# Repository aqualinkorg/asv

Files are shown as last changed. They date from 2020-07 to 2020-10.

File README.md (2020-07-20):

# Aqualink ASV

The Aqualink ASV is an open-source reference design for an autonomous surface vehicle. Included in this project are all hardware & electronics designs, software components, and instructions necessary to outfit a generic boat hull to navigate autonomously and collect camera and sensor data.

This project is designed around a collection of existing software projects, such as ROS2, Ardupilot, QGroundControl, and more. All hardware components are off-the-shelf with links to suppliers within the included [Bill of Materials](hardware/bill_of_materials.pdf) document. The construction process has been tailored to require no soldering and minimal, standard tools.

## Project Structure

The project is split into three main folders, each with their own setup guides:

- `groundstation/`: Contains setup instructions and software that will be run on a Linux laptop used to control the vehicle.
- `hardware/`: Contains all drawings & CAD (electrical and mechanical), assembly instructions and photos, and the bill of materials.
- `vehicle/`: Contains setup instructions and software for both the Nvidia Jetson Nano and Rambutan OpenWRT router that are installed in the vehicle electronics box.

While there is a great deal of flexibility in which order to read and follow the instructions, the order we recommend is:

1. Review all materials in `hardware/` to get an understanding of how everything fits together:
   - [Hardware Setup](hardware/README.md)
   - [System Diagram](hardware/drawings_and_cad/system_diagram.pdf)
   - [Electrical Connections](hardware/drawings_and_cad/electrical_connections.pdf)
   - [Bill of Materials](hardware/bill_of_materials.pdf)
2. Acquire all components, as specified by the BOM and your own project's requirements
3. Before assembling the hardware, set up the Nano and Rambutan router. These steps are easier pre-assembly:
   - [Nano Setup](vehicle/nano_setup.md)
   - [Router Setup](vehicle/router_setup.md)
4. Follow the instructions and drawings in the [Hardware Setup](hardware/README.md) to assemble the electronics and battery enclosures
5. Integrate the electronics and battery enclosures, motors, sensors, etc. into your vehicle hull
6. With the vehicle fully assembled, perform the [Pixhawk Setup](vehicle/pixhawk_setup.md)
7. At this point, your vehicle should be fully assembled, calibrated, and ready to deploy.

## Software Overview

Here is an image that shows the way all of the nodes connect together via ROS2 topics:

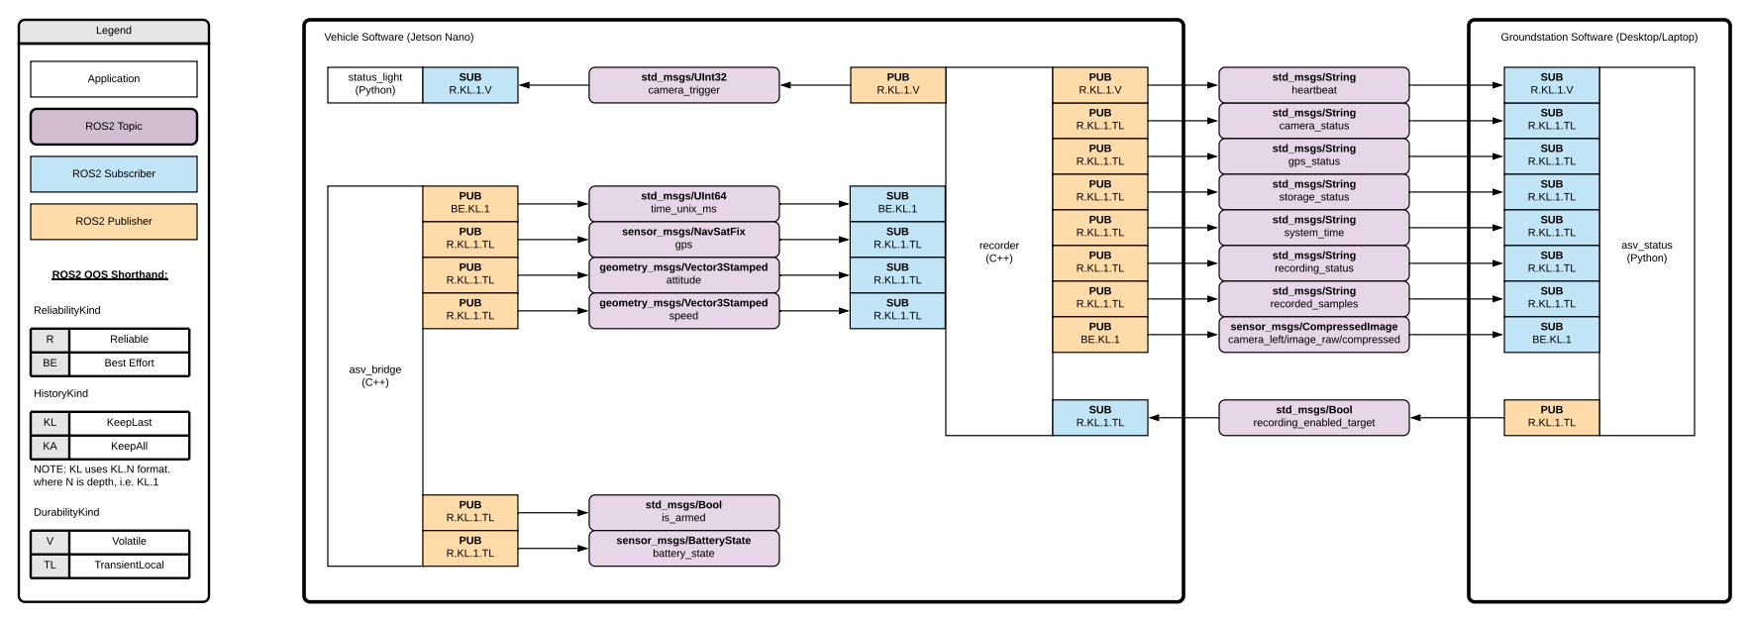
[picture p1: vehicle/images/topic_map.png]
topicmap


For more information on each software node, see:
  - [Groundstation Software](groundstation/README.md)
  - [Vehicle Software](vehicle/README.md)

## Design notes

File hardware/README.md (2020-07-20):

# Hardware Setup

## Pre-reqs
### Tools
- Drill + various drill bits (see drawings)
- Deburring tool (to clean up drill holes)
- Screwdriver set (phillips, slotted, hex)
- Crescent wrench (expands to at least 32mm)
- Needle nose pliers
- Scissors or flush cutters

### Parts
Refer to the [Bill of Materials (BOM)](bill_of_materials.pdf) for the list of parts

#### Not on Bill of Materials
- [Upper Plate](drawings_and_cad/upper_plate/) - This part can be laser cut out of 3mm thick material.
- [Power Mounting Block](drawings_and_cad/power_mounting_block/) - This part can be 3D printed
- Double sided tape (to secure Pixhawk)
- Grease (for o-rings)
- USB 3.0 SSD (for storing data)

## Assembly

### General Assembly Notes
- Make sure to lubricate all o-rings before installation
- M2.5x22mm screws (x4) are only used to attach the fan to the Jetson Nano

### Drill Enclosure
Refer to the [enclosure drawing](drawings_and_cad/enclosure/DRW-0023-01_PTS-25340-C_with_holes.pdf) for the location the holes should be drilled, as well as the hole diameter. The hole callouts are for clearance holes for parts to fit through. This means the sizes are less common. You can use a drill that is +/- 0.2mm without issue. Also, while all dimensions are metric, sometimes a standard drill bit will be a close match.

### Drill Bottom Plate
Refer to the [bottom plate drawing](drawings_and_cad/lower_plate/DRW-0019-01_PTV-25340_with_holes.pdf) for the location the holes should be drilled, as well as the hole diameter. The hole callouts are for clearance holes for parts to fit through. This means the sizes are less common. You can use a drill that is +/- 0.2mm without issue. Also, while all dimensions are metric, sometimes a standard drill bit will be a close match.

There are 3 sets of holes for the Eurostyle Terminal Block. This is to allow for some adjustment depending on wire length.

### Battery Tube Assembly
[Follow the Blue Robotics Guide](https://bluerobotics.com/learn/watertight-enclosure-assembly-guide/)

### Electrical Wiring
Follow the [System Diagram](drawings_and_cad/system_diagram.pdf) and [Electrical Connections](drawings_and_cad/electrical_connections.pdf) diagrams.

### Final Assembly
#### Enclosure Assembly
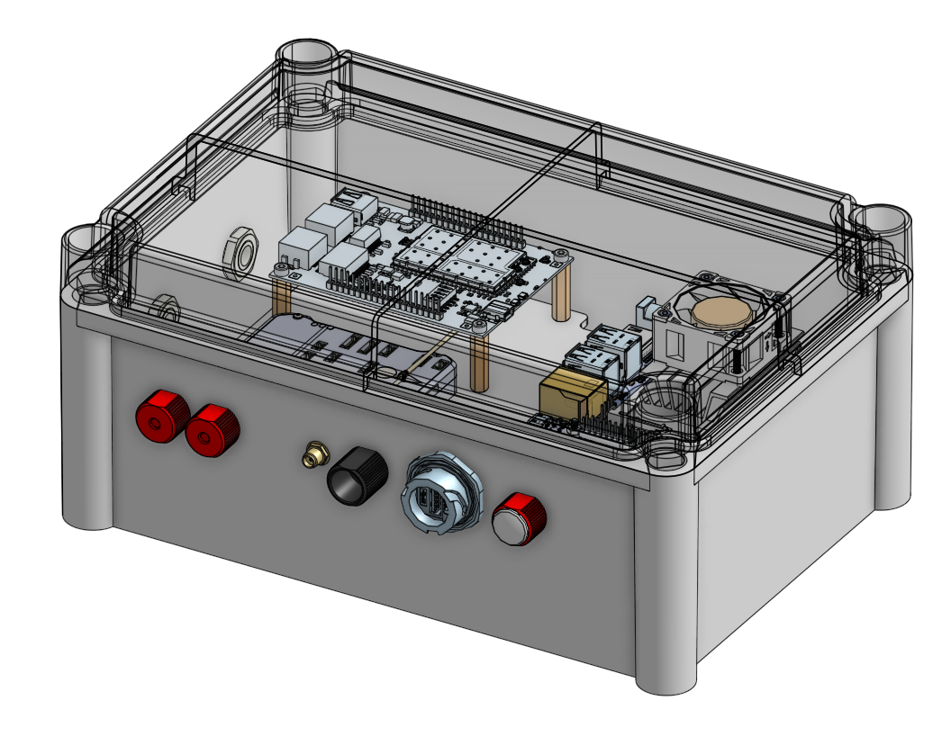
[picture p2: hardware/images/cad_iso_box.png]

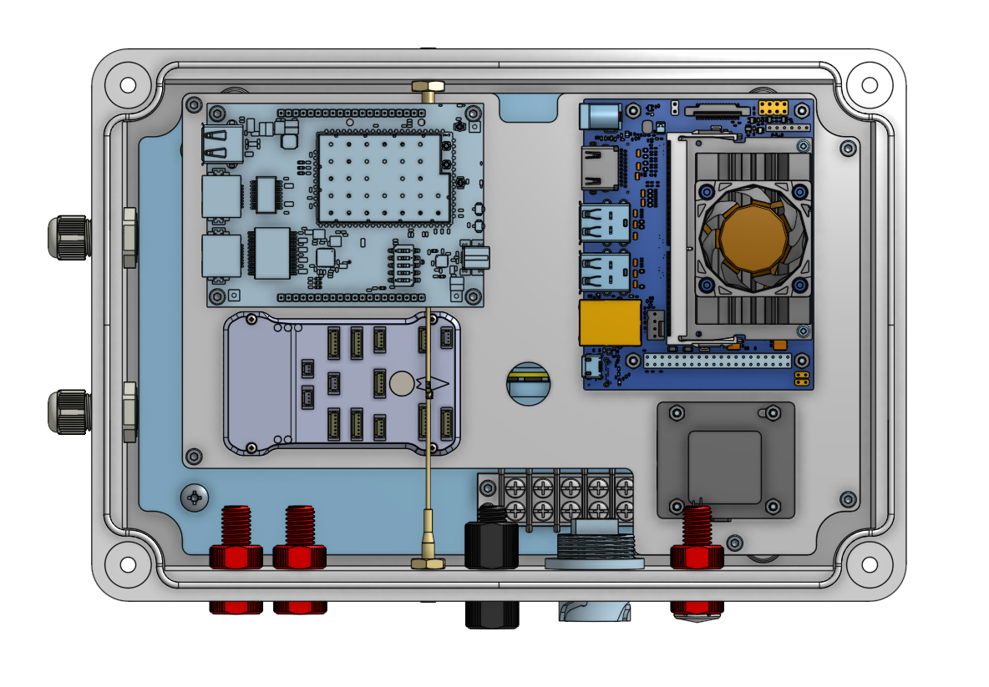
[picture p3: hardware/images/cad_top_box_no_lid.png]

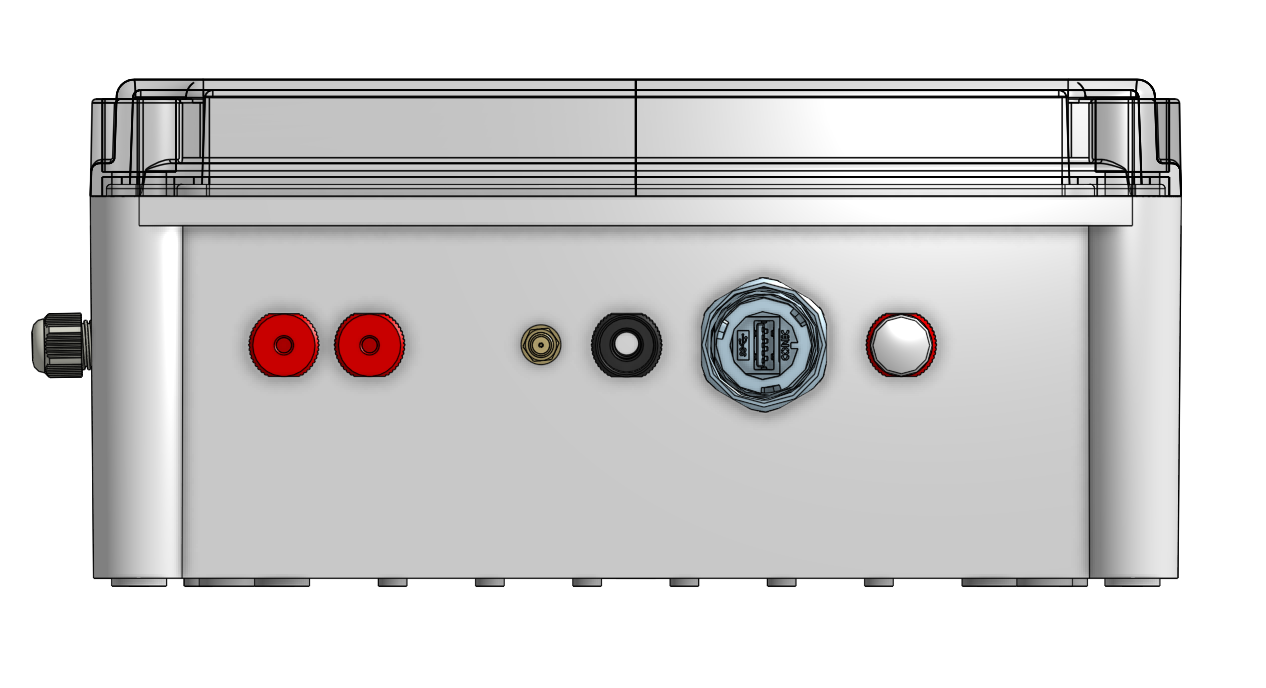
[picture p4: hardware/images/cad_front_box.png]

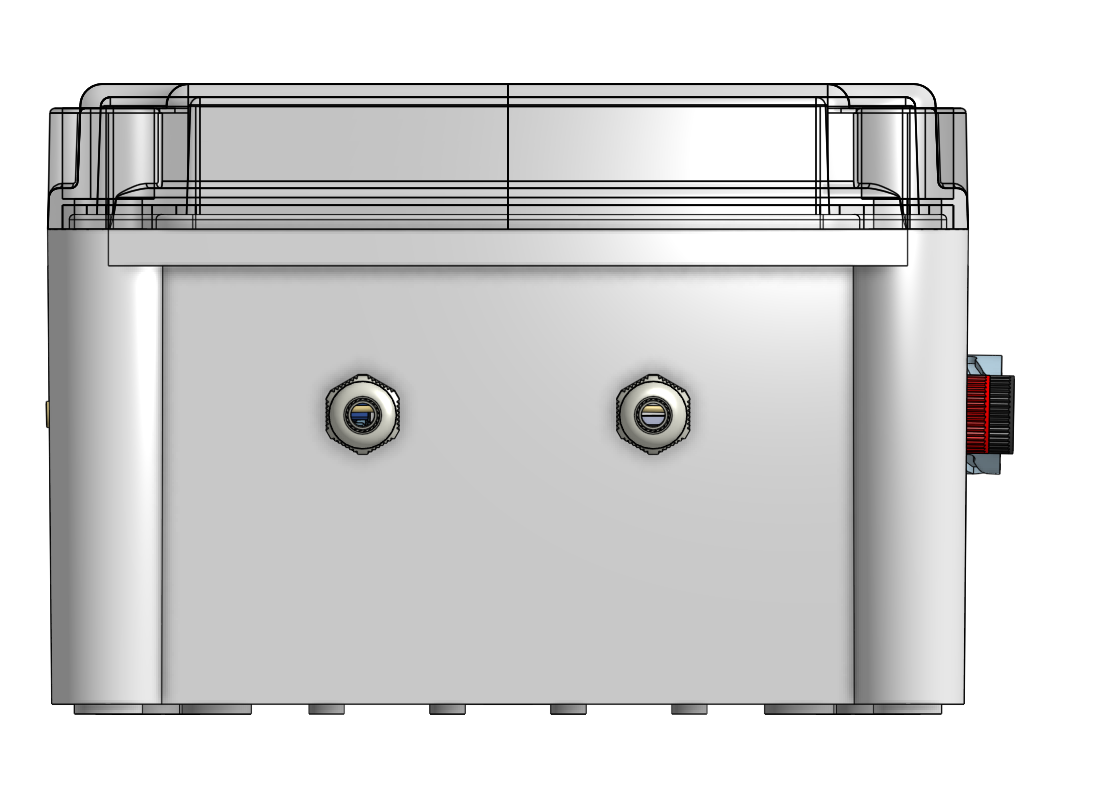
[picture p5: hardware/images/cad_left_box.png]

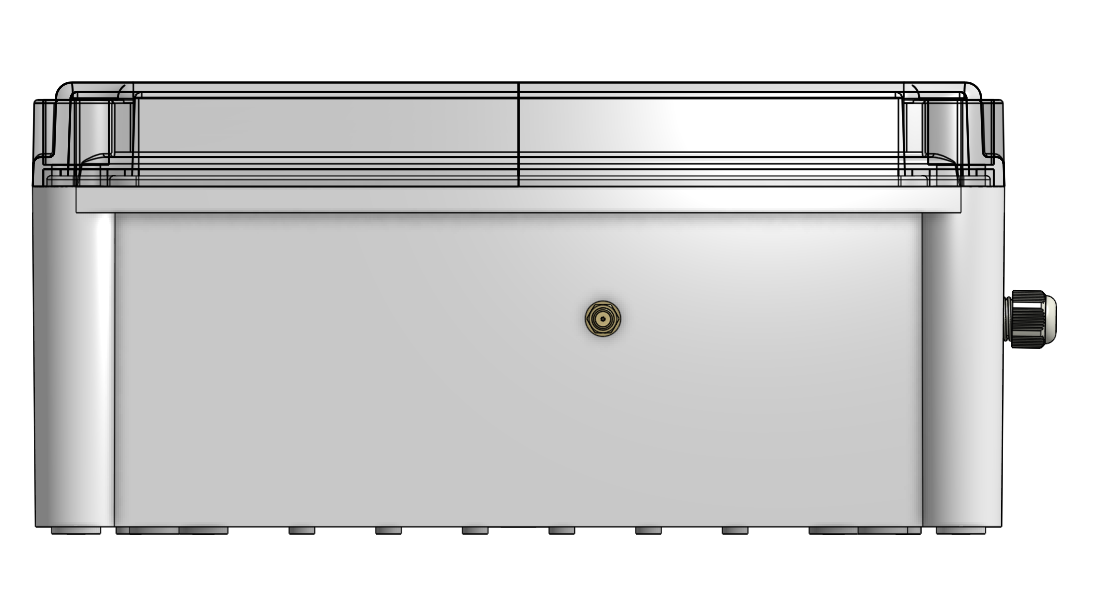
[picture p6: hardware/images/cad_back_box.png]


#### Plates Assembly
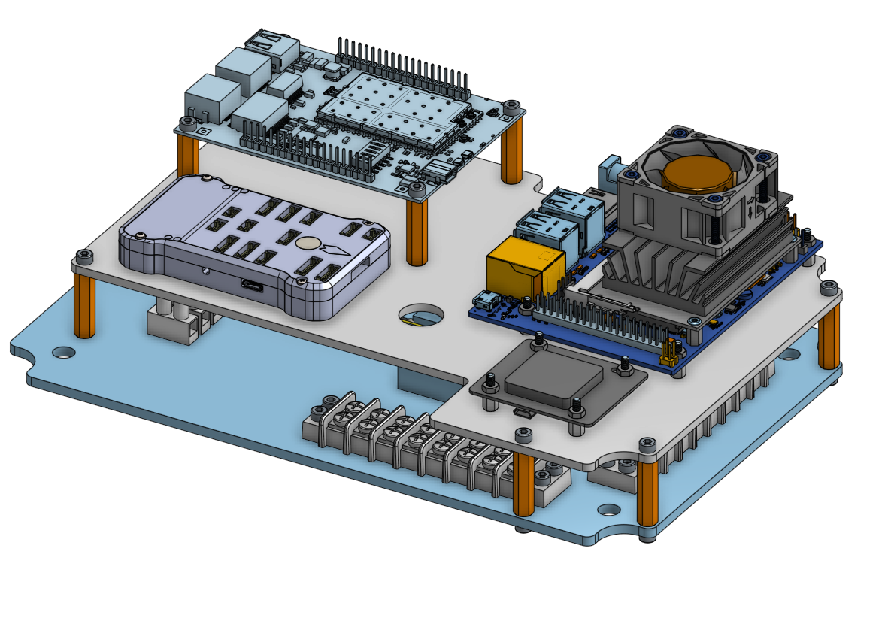
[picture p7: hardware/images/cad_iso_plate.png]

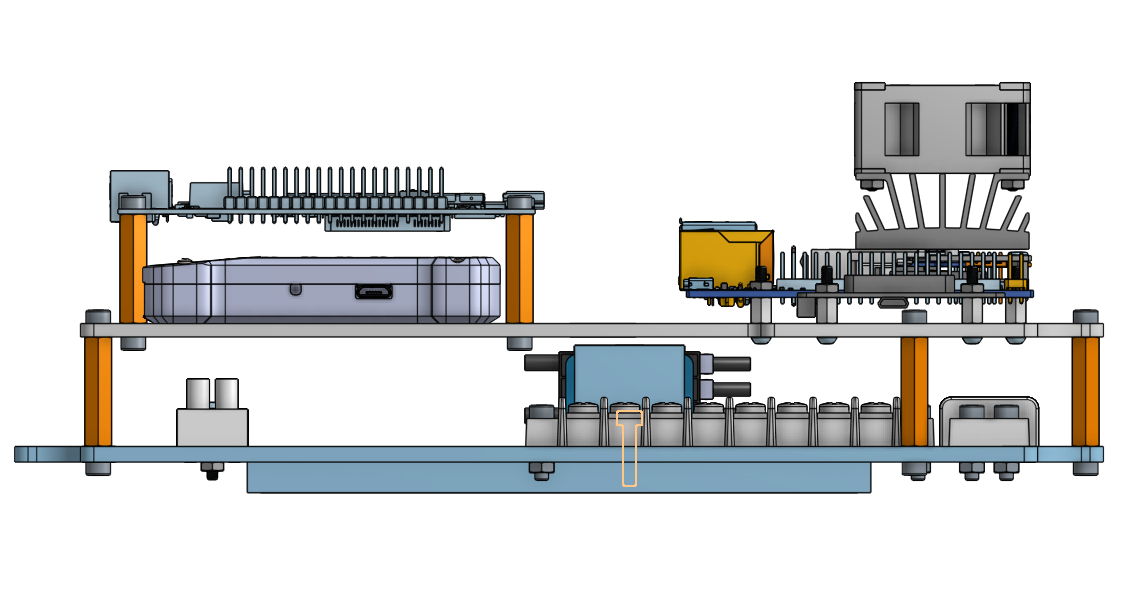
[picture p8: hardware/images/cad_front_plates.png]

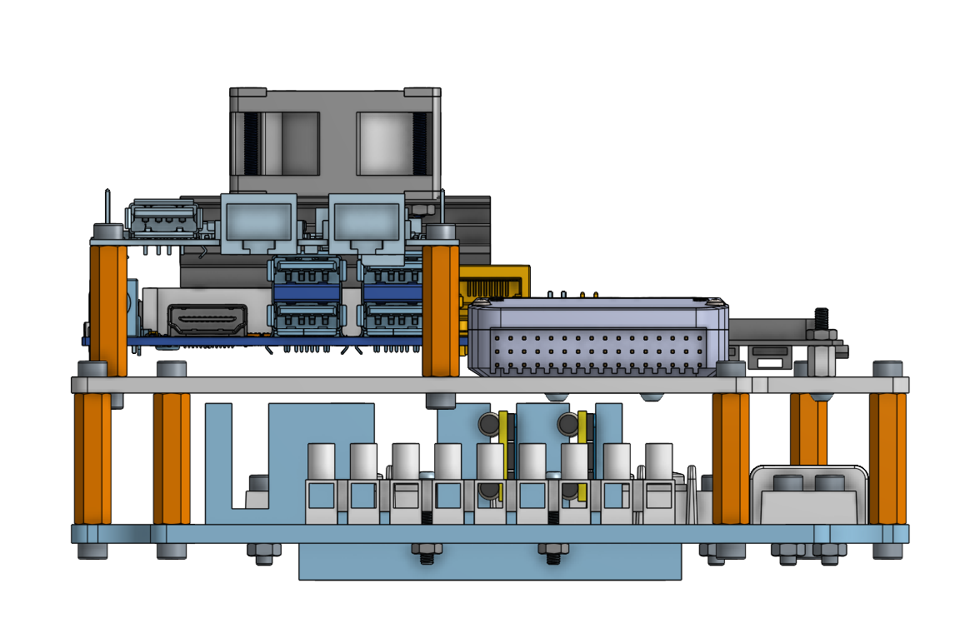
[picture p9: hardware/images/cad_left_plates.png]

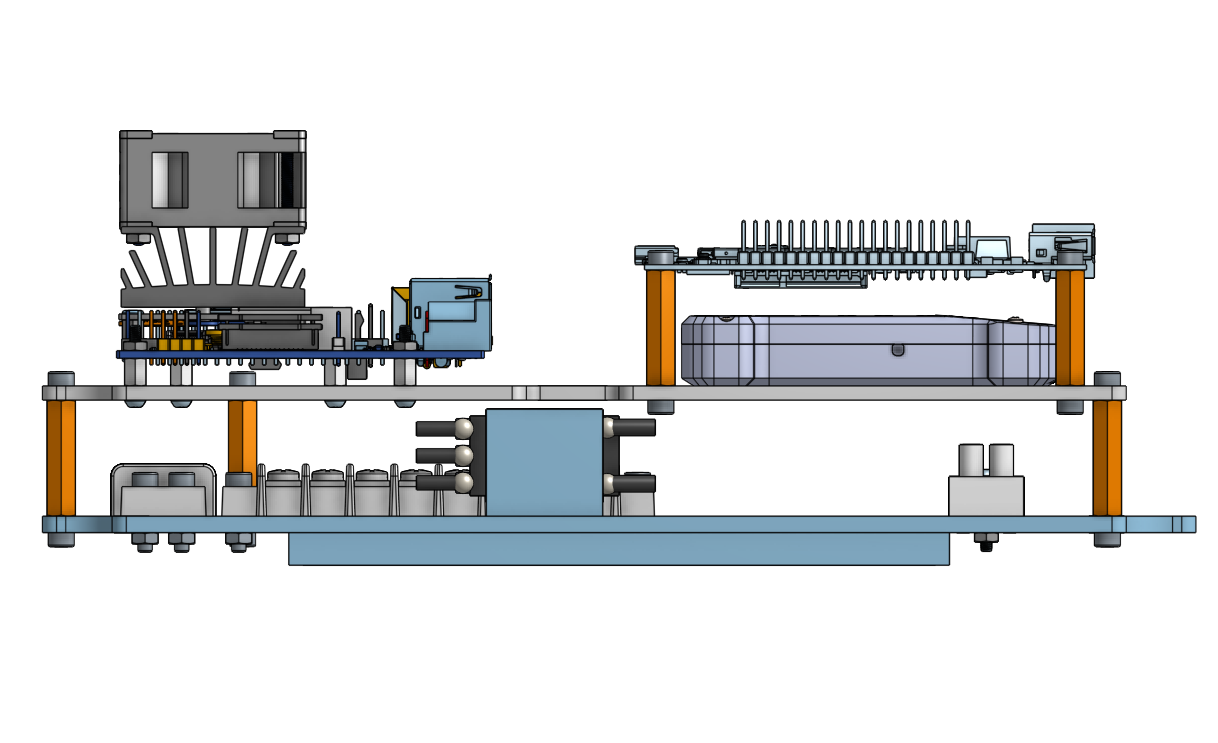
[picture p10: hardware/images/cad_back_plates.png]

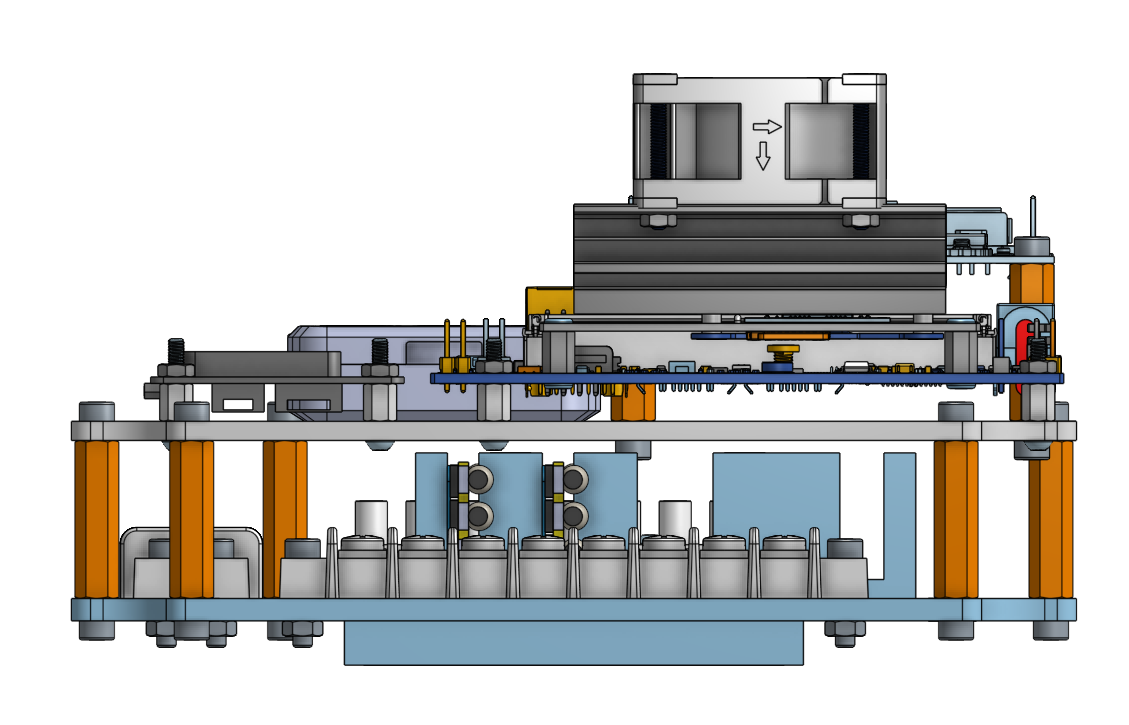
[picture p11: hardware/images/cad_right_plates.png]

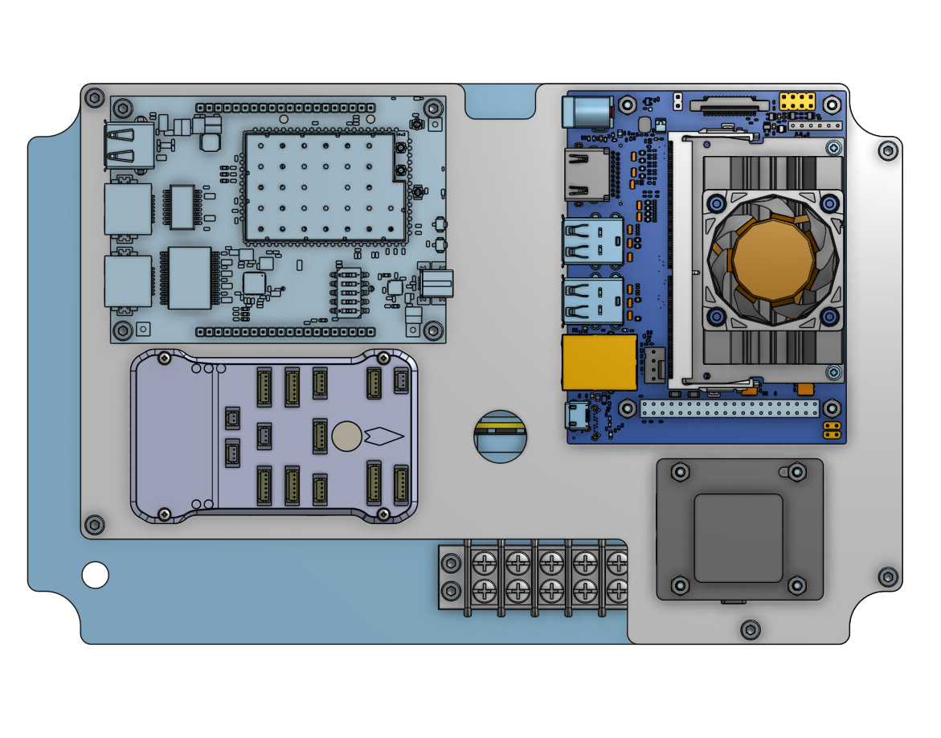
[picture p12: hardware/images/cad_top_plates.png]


#### Final Assembly Pictures
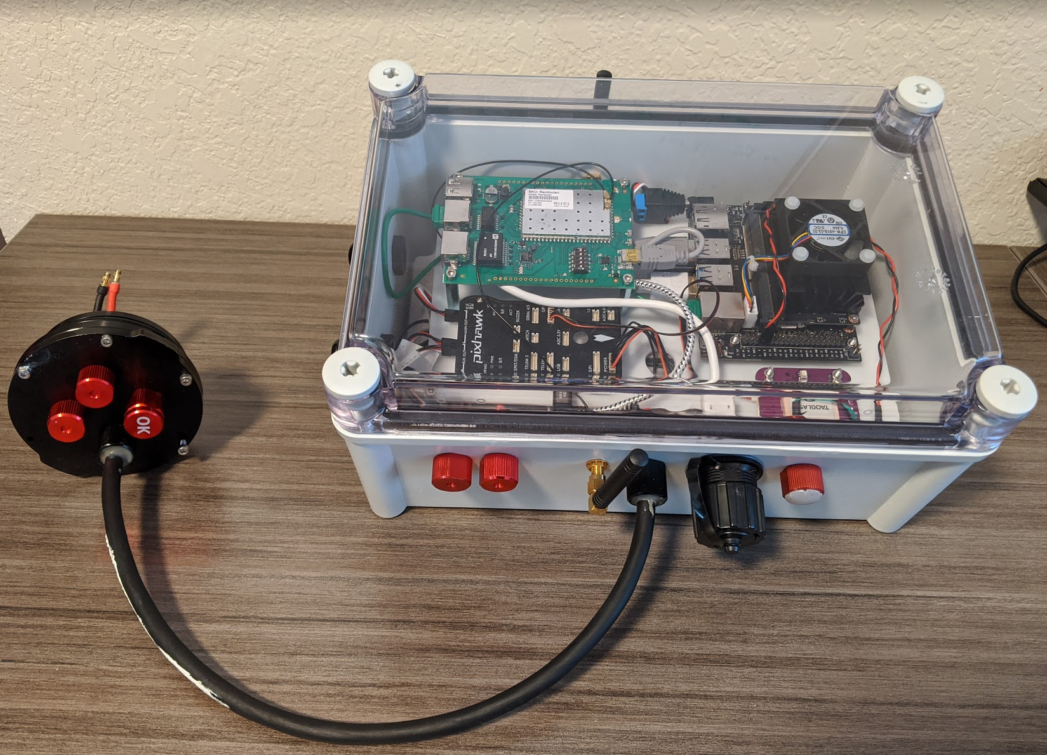
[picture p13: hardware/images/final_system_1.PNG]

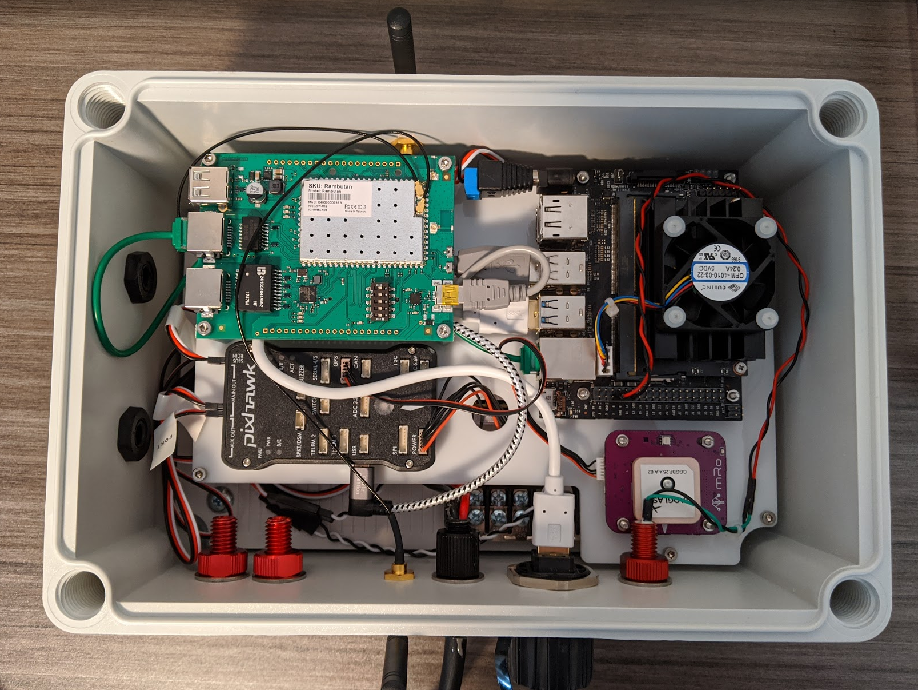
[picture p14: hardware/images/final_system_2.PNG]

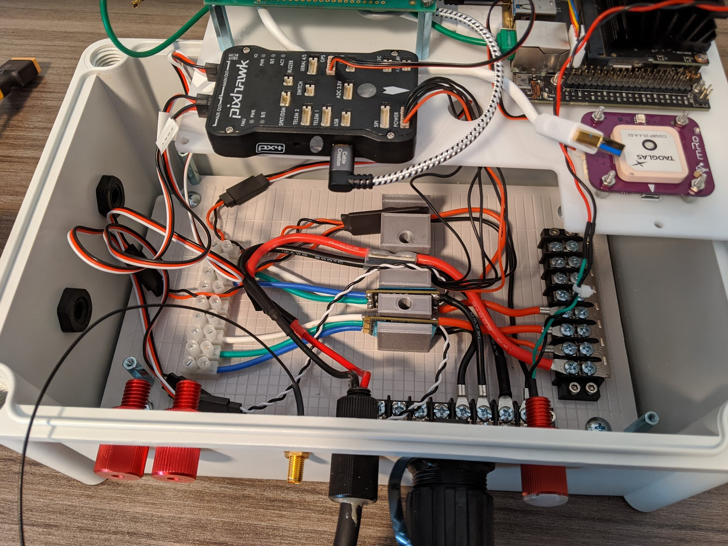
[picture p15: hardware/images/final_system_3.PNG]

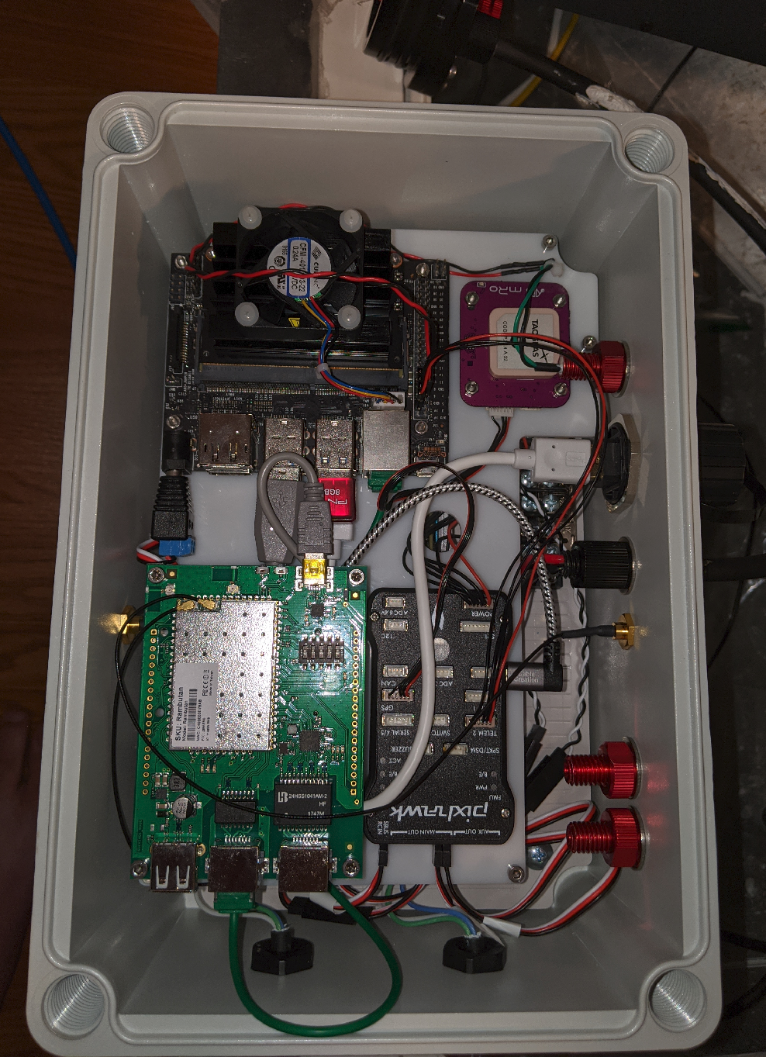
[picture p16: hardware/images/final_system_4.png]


### Other Notes
- The two blank penetrators are there for accessories that can be connected to the system.
- The antenna (RP-SMA) connectors on the side of the box can be replaced with cables and different antennas, depending on your use case.
- GPS should have clear view of the sky.
- Keep out of direct sunlight when powered on.

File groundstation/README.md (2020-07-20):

# Groundstation Software Overview

## ROS2 Nodes
There are two ROS2 nodes included in the groundstation software:

`asv_status`: A GUI application that allows you to monitor the vehicle, enable/disable recording of ZED2 and telemetry data on the vehicle, and see the camera stream. Below is a screenshot of asv_status in action:

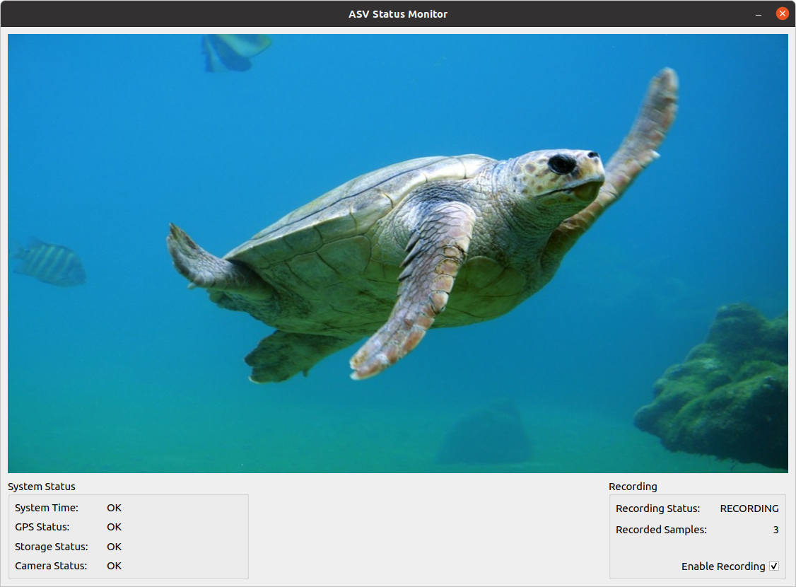
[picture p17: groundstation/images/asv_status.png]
asv_status


The items under System Status indicate the state of requirements necessary to enable recording of data. The system must sucessfully:

1. Receive a GPS time source
2. Attain a GPS fix
3. Find a valid location to store data in (as configured in recorder.yaml)
4. Successfully initialize the camera

Once all status elements read "OK" and the `Recording Status` on the right says "READY", you will be able to enable/disable recording by clicking the `Enable Recording` checkbox.

`mockbot`: An application that mimics the software running on the vehicle that can be used with `asv_status` to see how it works. Run this alongside `asv_status` on your desktop to get a preview of what will happen when the vehicle software is running.

## Ground Control Station

Additionally, the user is expected to use `QGroundControl`, a Qt-based Drone ground control station application, to configure and plan missions for the vehicle. For more information visit:

<http://qgroundcontrol.com/>

## Using ROS2 tools

Similarly to on the vehicle, you can use the ROS2 command line utilities to interact with any of the ROS2 nodes:

```bash
# Source the ROS2 Underlay
source /opt/ros/foxy/setup.bash

# Some commands
ros2 topic list
ros2 topic echo "gps"

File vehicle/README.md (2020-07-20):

# Vehicle (Nano) Software Overview

## Conan library packages

In: `vehicle/conan-packages`:

- `concurrentqueue`: threadsafe lockfree queue used by mavchannel
- `readerwriterqueue`: threadsafe lockfree queue used by mavchannel
- `serial`: serial port library used by mavchannel
- `mavchannel`: small library that combines serial, mavlink, and the threadsafe queues to provide a serial interface for devices that speak mavlink
- `mavlink2`: packaged version of the official mavlink repository. Mavlink is a communication protocol traditionally used within the Ardupilot/Ardusub space.

## ROS2 Nodes

There are three ROS2 nodes in the software package. Here is a short description of their functions:

- `asv_bridge`: This node bridges incoming Mavlink serial data from the Pixhawk to the ROS2 bus and vice-versa
- `recorder`: This node subscribes to telemetry data from the asv_bridge and captures frames from the ZED2 camera. When recording is enabled, it saves this data to disk.
  - This node also sends status info to the groundstation's `asv_status` node. The `asv_status` node lets you enable/disable recording.
- `status_light`: This node briefly flashes a status LED on the electronics enclosure each time a data sample is recorded by `recorder`.

There is one additional experimental ROS2 node called `pinger` which connects to the Blue Robotics Ping1D depth sounder module and publishes depth readings. This node is not thoroughly tested, nor is the data currently recorded by the `recorder` node, so individuals wishing to use this sensor should review and modify the code accordingly.

## Mavproxy

There is one additional process that runs at startup along with the ROS2 nodes, which is called `mavproxy`. `mavproxy` bridges the incoming mavlink serial communication coming from the Pixhawk to a UDP interface being used to communicate with QGroundControl on the groundstation computer. This allows QGroundControl to establish a telemetry and control link with the Pixhawk when the groundstation is connected to the vehicle's WiFi access point.

## Using ROS2 tools

You can use the ROS2 command line utilities to interact with the applications in this project:

```bash
# Source the ROS2 Underlay
source /opt/ros/eloquent/setup.bash

# Some commands
ros2 topic list
ros2 topic echo "gps"
```

See the official ROS2 docs for more info about what tools are available and how to use them.

## Interacting with the vehicle software manually

The software is automatically started on boot up by Systemd. Below are some commands you can use to manually interact with systemd:

```bash
# Start a service:
sudo systemctl start asv_bridge

# Stop a service:
sudo systemctl stop asv_bridge

# Restart a service
sudo systemctl restart asv_bridge

# Disable a service so it doesn't start at startup automatically:
sudo systemctl disable asv_bridge
```

Viewing real-time console logs of the applications can be done with journalctl:

```bash
# To view an entire log:
journalctl -u asv_bridge

# To trail a log in real-time
journalctl -u asv_bridge -f
```

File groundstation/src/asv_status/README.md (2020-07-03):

asv_status
============

A pointing device (e.g. mouse, touchpad) teleop tool for mobile robots,
supporting holonomic and differential drive platforms.

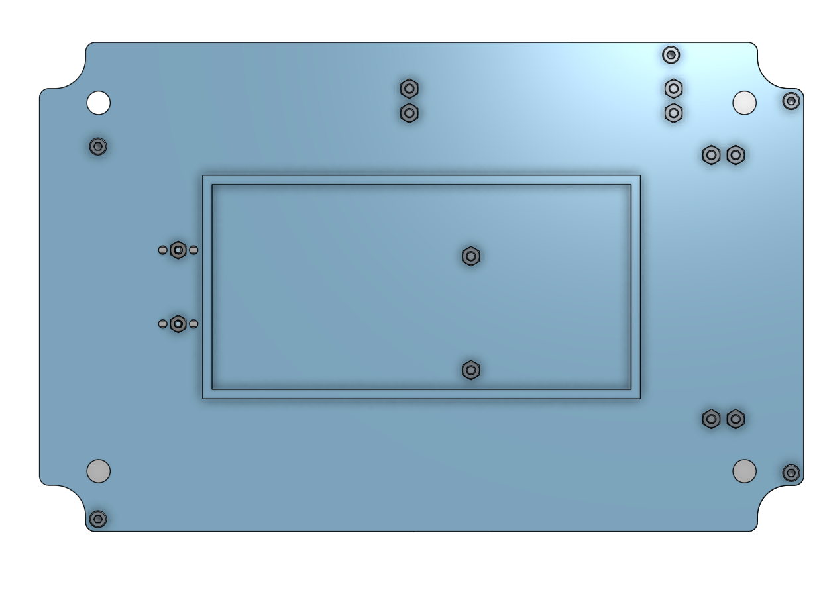
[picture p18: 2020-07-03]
hardware/images/cad_bottom_plates.png

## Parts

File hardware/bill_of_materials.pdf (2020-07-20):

Project - Surface Vehicle
Document - Bill of Materials (BOM) Revision - 4 (7/19/20)
Sub-System | Item | Vendor | Part Number | Qty. | Cost/Unit Extended Cost
Power | Lithium-ion Battery (14.8V, 18Ah) | Blue Robotics | BATTERY-LI-4S-18AH-R3-RP (https://bluerobotics.com/store/comm-control-power/powersupplies-batteries/battery-li-4s-18ah-r3/) | 1 | $289.00 | $289.00
| 5V 6A Power Supply | Blue Robotics | BEC-5V6A-R1 (https://bluerobotics.com/store/comm-control-power/elec-packages/bec-5v6a-r1/) | 1 | $22.00 | $22.00
| Power Sense Module | Blue Robotics | PSM-ASM-R2-RP (https://bluerobotics.com/store/comm-control-power/elec-packages/psm-asm-r2-rp/) | 1 | $31.00 | $31.00
Compute | NVIDIA Jetson Nano Developer Kit | Nvidia | Jetson Nano Developer Kit (https://developer.nvidia.com/buy-jetson?product=jetson_nano&location=US) | 1 | $99.00 | $99.00
| Noctua NF-A4x20 5V PWM, Premium Quiet Fan, 4-Pin, 5V Version
| (40x20mm, Brown) | Amazon | NF-A4x20 5V PWM | 1 | $14.95 | $14.95
| SanDisk Ultra 32GB MicroSDHC UHS-I Card | Amazon | SDSQUAR-032G-GN6MA (https://www.amazon.com/gp/product/B073JWXGNT/ref=ppx_yo_dt_b_asin_title_o02_s00?ie=UTF8&th=1) | 1 | $8.99 | $8.99
| Pixhawk 1 Flight Controller | Blue Robotics | PIXHAWK-R1-RP (https://bluerobotics.com/store/comm-control-power/elec-packages/pixhawk-r1-rp/) | 1 | $139.00 | $139.00
Connectivity (wifi) | Rambutan-DVK | 8devices | rambutan-dvk (https://shop.8devices.com/rambutan-dvk) | 1 | $79.00 | $79.00
| Highfine 2 x 6dBi 2.4GHz 5GHz Dual Band WiFi RP-SMA Antenna | Amazon | WIFI0006-ZJ (https://www.amazon.com/gp/product/B01GMBUS8O/ref=ppx_yo_dt_b_search_asin_title?ie=UTF8&psc=1) | 1 | $9.69 | $9.69
Cables and Connectors | Barrel Connector (5.5mm x 2.1mm DC Power Connector Adapter) | Amazon | B07SXKGLKJ (https://www.amazon.com/12V-DC-Power-Plug-Connector/dp/B07SXKGLKJ?th=1) | 1 | $6.98 | $6.98
| Female/Female Jumper Wires | Adafruit | 1950 (https://www.adafruit.com/product/1950#description) | 1 | $1.95 | $1.95
| Electronics Tray Terminal Blocks and Hardware | Blue Robotics | ETRAY4-CONN-R1-RP (https://bluerobotics.com/store/watertight-enclosures/etray4-conn-r1-rp/) | 1 | $35.00 | $35.00
| Battery Power Cable | Blue Robotics | BROV2-CAB-POWER-BULLET-CONNECTOR-R1-RP (https://bluerobotics.com/store/rov/bluerov2-components-spares/brov2-cab-power-bullet-connector-r1-rp/) | 1 | $46.00 | $46.00
| XT-90 Male to XT-60 Female | Amazon | B07YRRCR9G | 1 | $5.00 | $5.00
| XT-60 Male to 3.5mm Bullet Female | Amazon | B07MM9FGDP | 1 | $3.00 | $3.00
| mRo 6-Pins JST-GH to 6-Pins DF13 | mRobotics | MRC0203 | 1 | $4.90 | $4.90
| USB3.0 Male to Male Cable 1ft, SNANSHI USB 3.0 Cable Cord
| Type A Male to A Male Cable USB to USB Cable in White | Amazon | B01M719D7Q | 1 | $5.99 | $5.99
| 3-Pin Servo Extension Lead Wire Cable Cord for Control Board Remote Control Parts, Female to Male, 320 mm (12 Pieces) | Amazon | B06XCRSD3T | 1 | $7.99 | $7.99
| StarTech.com 6 in. USB to Mini USB Cable - USB 2.0 A to Mini B - Gray - Mini USB Cable (USB2HABM6IN) | Amazon | USB2HABM6IN | 1 | $7.44 | $7.44
| CableCreation [2-Pack] Short Left Angle USB 2.0 Cable, 90 Degree
| USB 2.0 A to Micro USB Cable, Compatible Chromecast, Power
| Pack, Samsung Galaxy Tab, Aluminium Case, 0.5FT | Amazon | CC0541 | 1 | $6.99 | $6.99
| Micro SlimRun Cat6 Ethernet Patch Cable - Stranded, 550MHz,
| UTP, Pure Bare Copper Wire, 32AWG, 1ft, Green | Monoprice | 34223 | 1 | $1.69 | $1.69
| MRC0257 - [6-Pins DF13] to [4-Pins 2.54mm header] - 200mm | mRobotics | MRC0257 (https://store.mrobotics.io/product-p/mrc0257.htm) | 1 | $2.86 | $2.86
Cable Passthroughs | USB Bulkhead | Mouser | 17-241001 | 1 | $16.28 | $16.28
| Blank penetrator | Blue Robotics | PENETRATOR-M-BLANK-10-25-R3-RP | 2 | $4.00 | $8.00
| CABLE GLAND 3-6.5MM M12 NYLON | Digikey | AIO-CSM12 | 2 | $1.41 | $2.82
| Antenna bulkhead cable | Digikey | 336320-12-0250 | 2 | $17.33 | $34.66
Actuation | T200 Thruster | Blue Robotics | T200-THRUSTER-R1-RP (https://bluerobotics.com/store/thrusters/t100-t200-thrusters/t200-thruster/) | 2 | $179.00 | $358.00
| Basic ESC | Blue Robotics | BESC30-R3 (https://bluerobotics.com/store/thrusters/speed-controllers/besc30-r3/) | 2 | $27.00 | $54.00
| Subsea LED Indicator | Blue Robotics | INDICATOR-ASM-BLUE-R1-RP (https://bluerobotics.com/store/thrusters/lights/indicator10-asm-r1/) | 1 | $13.00 | $13.00
Sensors | mRo GPS u-Blox Neo-M8N | mRobotics | MRO-GPS003-MR | 1 | $66.90 | $66.90
| ZED 2 Stereo Camera | Stereo Labs | ZED 2 Stereo Camera (https://store.stereolabs.com/products/zed-2) | 1 | $449.00 | $449.00
Mechanical (Electronics) | Bud Industries BOX PLASTIC GRY/CLR 11"LX7.48"W | DigiKey | PTS-25340-C (https://www.digikey.com/products/en?keywords=PTS-25340-C) | 1 | $42.20 | $42.20
| Bud Industries PTS MOUNTING PLATE PLASTIC | Mouser | PTX-25340-P | 1 | $3.50 | $3.50
Mechanical (Battery) | Cast Acrylic Tube – 11.75″, 298mm (3″ Series) | Blue Robotics | WTE3-P-TUBE-12-R1-RP (https://bluerobotics.com/store/watertight-enclosures/3-series/wte3-p-tube-12-r1/) | 1 | $86.00 | $86.00
| O-Ring Flange (3″ Series) | Blue Robotics | WTE3-M-FLANGE-SEAL-R2-RP (https://bluerobotics.com/store/watertight-enclosures/3-series/o-ring-flange-3-series/) | 2 | $24.00 | $48.00
| Aluminum End Cap with 4 Holes (3″ Series) | Blue Robotics | WTE3-M-END-CAP-4-HOLE-R1-RP (https://bluerobotics.com/store/watertight-enclosures/3-series/wte3-m-end-cap-4-hole-r1/) | 1 | $12.00 | $12.00
| Aluminum End Cap (3″ Series) | Blue Robotics | WTE3-M-END-CAP-R1-RP (https://bluerobotics.com/store/watertight-enclosures/3-series/wte3-m-end-cap-r1/) | 1 | $10.00 | $10.00
| Enclosure Clamp (3″ Series) | Blue Robotics | WTE3-M-CLAMP-R1-RP (https://bluerobotics.com/store/watertight-enclosures/3-series/enclosure-clamp-3-series/) | 1 | $36.00 | $36.00
Accessories | Lithium Battery Charger | Blue Robotics | BATTERY-CHARGER-0620AC-US-R1 (https://bluerobotics.com/store/comm-control-power/powersupplies-batteries/lithium-battery-charger/) | 1 | $149.00 | $149.00
Hardware | Female-Female Hex Standoff, 6mm Hex, 25mm Long, M3 x 0.5mm
| Thread | McMaster | 92080A713 | 9 | $3.18 | $28.62
| Female-Female Hex Standoff, 4.5mm Hex, 6mm Long, M2.5 x 0.45 mm Thread | McMaster | 92080A001 | 8 | $0.78 | $6.24
| Socket Head Screw, M3 x 0.5 mm Thread, 14 mm Long (Pack of
| 50) | McMaster | 92290A118 | 1 | $5.33 | $5.33
| Hex Nut M3 x 0.5 mm Thread (Pack of 50) | McMaster | 94150A325 | 1 | $3.08 | $3.08
| Button Head Hex Drive Screw, M2.5 x 0.45 Thread Size, 16mm
| Long (Pack of 100) | McMaster | 92095A114 | 1 | $4.88 | $4.88
| Hex Nut M2.5 x 0.45 mm Thread (Pack of 50) | McMaster | 94150A310 | 1 | $3.69 | $3.69
| Socket Head Screw, M2.5 x 0.45 mm Thread, 22 mm Long (Pack of
| 25) | McMaster | 91292A312 | 1 | $8.50 | $8.50
| General Purpose Washer, for M2.5 Screw Size, 2.700 mm ID, 5 mm
| OD (Pack of 100) | McMaster | 98689A111 | 1 | $2.57 | $2.57
| | | | | Total | $2,280.68

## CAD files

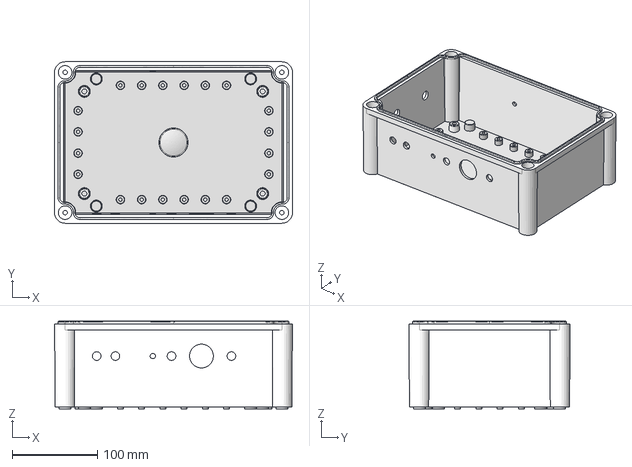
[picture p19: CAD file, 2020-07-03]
hardware/drawings_and_cad/enclosure/PRT-0020-01_PTS-25340-C_with_holes.step
280.0 x 190.0 x 103.0 mm

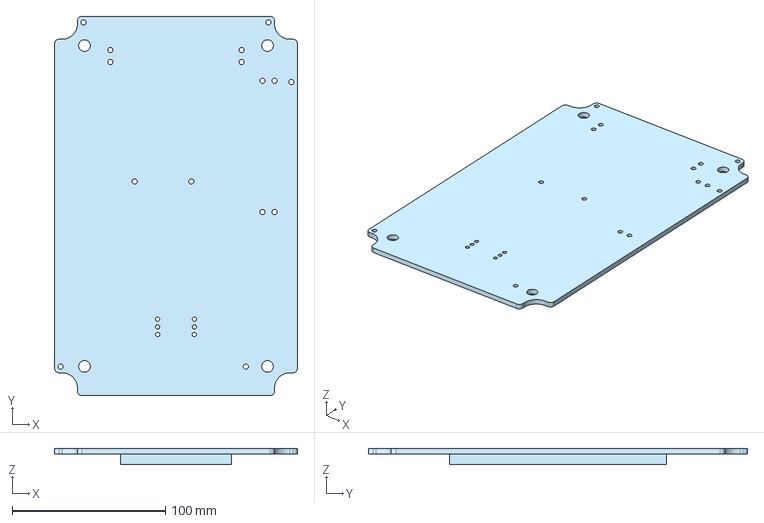
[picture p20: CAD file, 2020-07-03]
hardware/drawings_and_cad/lower_plate/PRT-0018-01_PTX-25340-P_with_holes.step
158.8 x 247.9 x 10.5 mm

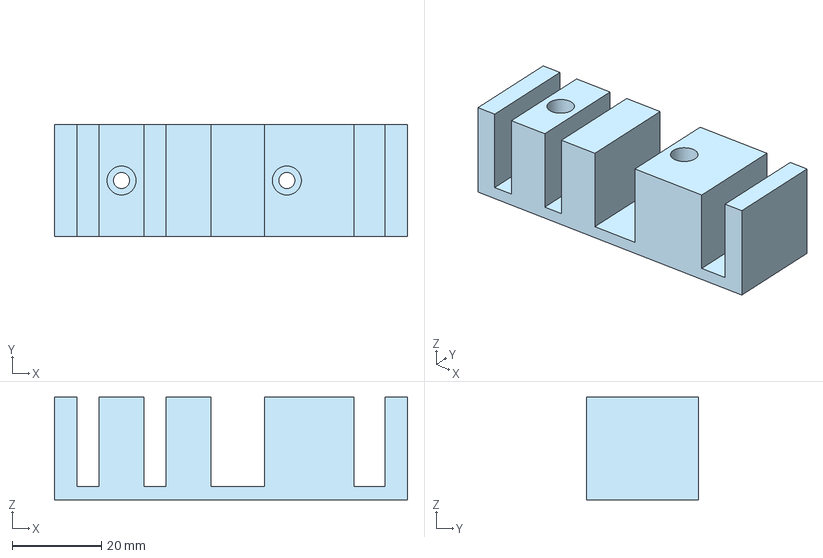
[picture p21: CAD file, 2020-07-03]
hardware/drawings_and_cad/power_mounting_block/PRT-0015-10_power_mounting_block.step
79.0 x 25.0 x 23.0 mm

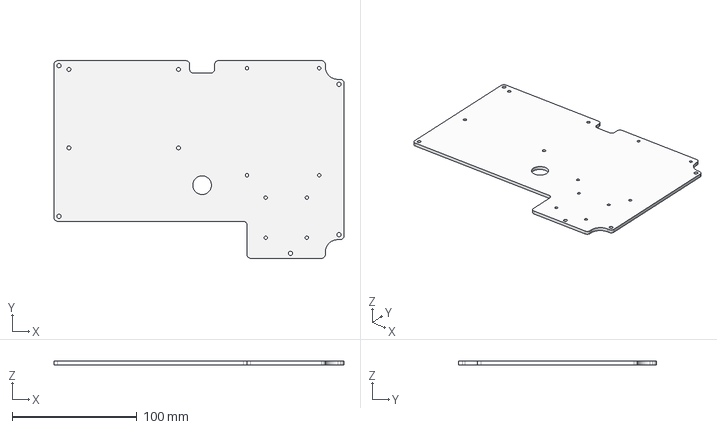
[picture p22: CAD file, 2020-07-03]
hardware/drawings_and_cad/upper_plate/PRT-0013-01_upper_plate.step
232.9 x 158.7 x 3.00 mm

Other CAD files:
hardware/drawings_and_cad/power_mounting_block/PRT-0015-10_power_mounting_block.stl
hardware/drawings_and_cad/upper_plate/PRT-0013-01_upper_plate.dxf

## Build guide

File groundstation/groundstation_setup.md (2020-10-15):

# Development and Operation PC Setup

For this tutorial, we will be using Ubuntu 20.04. Everything we do here is also generally supported on Ubuntu 18.04, but requires some manual steps to install the correct versions of dependencies, whereas Ubuntu 20.04 has everything we need readily available.

Furthermore, you can also achieve a working setup on OSX and Windows, as ROS2, Python, and OpenCV, and Qt are all available on these platforms, but such efforts will be considered out of scope and left as an exercise to the reader.

## Installing ROS2 & Dependencies

We will generally be following, with a few additional items:

<https://index.ros.org/doc/ros2/Installation/Foxy/Linux-Install-Debians/>

```sh
# Install utilities needed for next steps
sudo apt-get update
sudo apt-get install curl gnupg2 lsb-release

# Add ROS2 repositories to your apt source lists
curl -s https://raw.githubusercontent.com/ros/rosdistro/master/ros.asc | sudo apt-key add -
sudo sh -c 'echo "deb [arch=$(dpkg --print-architecture)] http://packages.ros.org/ros2/ubuntu $(lsb_release -cs) main" > /etc/apt/sources.list.d/ros2-latest.list'
sudo apt-get update

# Install ROS2 Foxy Fitzroy release (2020 LTS release), as well as additional supporting python packages
sudo apt-get install \
    python3-argcomplete \
    python3-colcon-common-extensions \
    python3-opencv \
    python3-rosdep \
    python3-vcstool \
    python3-wheel \
    ros-foxy-desktop

# Install development tools (some of these may have already been installed)
sudo apt-get install \
    build-essential \
    cmake \
    git

# Install Qt5 and PyQt5
sudo apt-get install \
    pyqt5-dev-tools \
    python3-pyqt5 \
    qtcreator \
    qttools5-dev-tools
```

Test to make sure ROS2 installation is functional by running the following commands and making sure ROS2 utilities run:

```sh
source /opt/ros/foxy/setup.bash
ros2 topic list
```

## Installing QGroundControl

Next, we will install QGroundControl, an application that serves as a groundstation for Pixhawk-based drones, and others. QGroundControl can be used out of the box to plan autonomous surveys and send them to your vehicle to execute. It also is required to set up a few configuration items for your vehicle.

Follow the instructions provided here:
<https://docs.qgroundcontrol.com/en/getting_started/download_and_install.html#ubuntu>

## Downloading and building the OpenASV software

First, choose a location to clone the OpenASV repository, then navigate there in a terminal. From that location, you can run the following commands to download and build the software:

```bash
# Download the software
git clone https://github.com/oceansystems/asv

# Build the groundstation software
cd asv/groundstation
./build.sh
```

## Running the software

To run the software, simply run the run_*.sh script from the groundstation/scripts/ directory for the application you wish to run, i.e.

```bash
# In one terminal, run mockbot:
./asv/groundstation/scripts/run_mockbot.sh

# In another terminal, run asv_status:
./asv/groundstation/scripts/run_asv_status.sh
```

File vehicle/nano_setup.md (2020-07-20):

# Preparing your Jetson Nano image

When setting up the Jetson Nano, you will need a monitor, keyboard, mouse, and internet connection provided directly to the Nano. We recommend performing this setup before installing the Rambutan in your electronics box. This will give you room to plug in HDMI and USB cables for the setup process. If you don't have the ability to provide an ethernet connection to the internet (i.e. you only have WiFi), you will need a USB WiFi adapter. Some adapters do not work out of the box with the Nano as they lack compatible drivers. Be sure to check that the adapter you intend to use is supported before making any purchases.

## Creating an SD card with a working image

First, you will need to create a bootable SD card and set up your Jetson Nano, following the guide found here:
<https://developer.nvidia.com/embedded/learn/get-started-jetson-nano-devkit#intro>

As an additional resource, which includes some more detail, you can read:
<https://www.pyimagesearch.com/2020/03/25/how-to-configure-your-nvidia-jetson-nano-for-computer-vision-and-deep-learning/>

*NOTE:* At the time of writing this guide, the latest version available was 32.4.2, which includes Ubuntu 18.04 and CUDA 10.2.
The rest of this guide will assume the use of these versions.

## Software Setup

After finishing the hardware and SD image setup process, make sure you have an internet connection, power on the Nano and walk through the following commands in a terminal:

```bash
# First, update pre-installed software
sudo apt-get update
sudo apt-get upgrade

# Next we will install some basic tools and dependencies that we will need:
sudo apt-get update -y
    sudo apt-get install -y --no-install-recommends \
        apt-transport-https \
        apt-utils \
        build-essential \
        cmake \
        curl \
        git \
        gnupg2 \
        less \
        libv4l-dev \
        libxml2-dev \
        libxslt1-dev \
        lsb-release \
        nano \
        openssh-server \
        python3-pip \
        sudo \
        supervisor \
        udev \
        vim \
        wget

# Install ROS2 Eloquent:
# Note: We have to use Eloquent for now, because Foxy is only supported on Ubuntu 20.04, which isn't released for the Nano at the time of writing this guide.

# Set up apt sources list
curl -s https://raw.githubusercontent.com/ros/rosdistro/master/ros.asc | sudo apt-key add -
sudo sh -c 'echo "deb [arch=$(dpkg --print-architecture)] http://packages.ros.org/ros2/ubuntu $(lsb_release -cs) main" > /etc/apt/sources.list.d/ros2-latest.list'

# Install ROS2 Eloquent and some additional packages
sudo apt-get update -y
sudo apt-get install -y --no-install-recommends \
    ros-eloquent-ros-base \
    python3-argcomplete \
    python3-colcon-common-extensions \
    python3-rosdep \
    python3-vcstool \
    python3-wheel

# Install packages required to run mavproxy and status_light services
sudo -H pip3 install mavproxy Jetson.GPIO bluerobotics-ping

# Install Conan C++ package manager (used to build software)
pip3 install conan==1.26.1

# Add user and usr/local bin folders to PATH, so you can run conan
echo "PATH=\"\${PATH}:/home/${USER}/.local/bin:/usr/local/bin\"" >> ~/.bashrc
source ~/.bashrc

## ----------------------
# Set up various permissions and rules to make sure all files, cameras, and serial ports can be accessed

# Change permissions on /opt so you can write to it as a non-root user
sudo chown -R ${USER}:${USER} /opt

# First add your user to necessary groups
sudo usermod -a -G video ${USER}
sudo usermod -a -G tty ${USER}
sudo usermod -a -G dialout ${USER}

# Disable console on /dev/ttyTHS1 (pre-enabled on stock Nano images)
sudo systemctl stop nvgetty
sudo systemctl disable nvgetty

# Add udev rule to allow non-root access on /dev/ttyTHS* serial devices
sudo sh -c "echo 'KERNEL==\"ttyTHS*\", MODE=\"0666\"' > /etc/udev/rules.d/55-tegraserial.rules"

## -----------------------

# Download the ZED SDK that matches the Jetpack 4.4, CUDA 10.2 release on the Nano
curl -O https://stereolabs.sfo2.cdn.digitaloceanspaces.com/zedsdk/3.2/ZED_SDK_Tegra_JP44_v3.2.0.run

# Make the installer executable
chmod +x ZED_SDK_Tegra_JP44_v3.2.0.run

# Run and follow the instructions. Enter 'y' for all y/n prompts and leave values as their default
./ZED_SDK_Tegra_JP44_v3.2.0.run

# The output should look something like:

  # Verifying archive integrity...  100%   All good.
  # Uncompressing 'ZED camera SDK by Stereolabs'  100%  
  # Installing...
  # To continue you have to accept the EULA. Accept  [Y/n] ?y
  # Installing...
  # Installation path: /usr/local/zed
  # [sudo] password for youruser:
  # Checking CUDA version...
  # OK: Found CUDA 10.2
  # Do you want to install the static version of the ZED SDK [Y/n] ?y
  # Do you want to install the Object Detection module (recommended), cuDNN and TensorRT will be installed [Y/n] ?y
  # Install samples (recommended) [Y/n] ?y
  # Installation path: /usr/local/zed/samples/
  # Do you want to auto-install dependencies (recommended) ? following packet will be installed via the package manager : libjpeg-turbo8 libturbojpeg libusb-1.0 libopenblas-dev libv4l-0 curl unzip libpng-dev libglew-dev freeglut3-dev qt5-default libqt5opengl5 libqt5svg5 [Y/n] ?y
  # ...
  # Dependencies installation complete
  # ZED SDK installation complete !

# After successfully installing the ZED SDK, *WITH* the camera connected, run the following, which will open a GUI and also download the calibration file for your specific camera:
/usr/local/zed/tools/ZED_Explorer

# Now that everything has been installed, reboot so that certain modifications take effect
sudo reboot now
```

## Download and Build the OpenASV Software

Similar to the groundstation setup, we need to clone and build the software. *NOTE:* There are a few additional steps involved.

```bash
# Download the software to the /opt/openasv directory
git clone https://github.com/oceansystems/asv /opt/openasv

# Navigate to the software directory
cd /opt/openasv/vehicle

# Install systemd service files
sudo cp -a ./res/systemd/. /lib/systemd/system/

# Install conan configuration
mkdir -p ~/.conan/profiles
cp /opt/openasv/vehicle/res/conan/default ~/.conan/profiles/

# Build the conan dependencies
# NOTE: This will take some time on the first run
cd /opt/openasv/vehicle/conan-packages
./build.sh  

# Build the vehicle software
# NOTE: This will take some time on the first run
cd /opt/openasv/vehicle/src
./build.sh

# Once the software is successfully built, enable the installed systemd service files for the software
sudo systemctl enable asv_bridge
sudo systemctl enable mavproxy
sudo systemctl enable recorder
sudo systemctl enable status_light
```

## Setting up a USB flash drive for data storage

We will want to make sure that when using a USB flash drive, the drive is always automatically mounted at boot and mounts to a consistent filesystem location, so our software can locate it.

First, format a flash drive using your preferred method. We recommend using the FAT32 format and the following instructions will assume a drive formatted to FAT32.

Once you have a USB drive formatted to FAT32, plug it into a free USB port on the Nano. Next, follow these steps:

```bash
# With your USB drive plugged in, run:
sudo blkid

# Look for your flash drive in the output of the previous command. \
# As an example, for a flash drive with a label name of "CYBIE", this is returned:
# /dev/sda1: LABEL="CYBIE" UUID="B668-998A" TYPE="vfat" PARTUUID="e1ee37e1-01"

# Create a variable with the UUID information for your device. As an example:
export USB_UUID="B668-998A"

# Copy the UUID value and add it to your /etc/fstab file in the following manner:
sudo sh -c "UUID=${USB_UUID} /media/${USER}/usb vfat rw,nofail,umask=022,uid=1000,gid=1000 0 0"

# Create the directory and change its permissions
sudo mkdir -p /media/${USER}/usb
sudo chown ${USER}:${USER} /media/${USER}/usb

# Reboot to get the above changes to take effect and then verify that the device is successfully mounted by writing a file to it and checking it on another device
sudo reboot now
```

## Configuring the data recording location for the ASV software

In general, you will want to configure your software to write data to a USB3 flash drive, such that you don't accidentally fill up the Nano's main filesystem. This will also allow you to easily offload the recordings, which can quickly grow to several gigabytes in size.

To configure the storage location, modify the `/opt/openasv/vehicle/src/recorder/config/recorder.yaml` file, which has contents that default to:

```yaml
recorder:
  ros__parameters:
    minimum_sample_period_msecs: 2000
    storage_path: "/tmp"
```

If you configured your USB drive to mount to /media/${USER}/usb, set the storage_path variable to match that (replacing ${USER} with your actual username).

If you like, you can also modify the minimum period that `recorder` records samples at. By default, `recorder` will record samples no faster than once every 2000ms (recording is triggered on the earliest GPS update that happens after this period). By increasing the minimum period, you can control how quickly your storage disk space fills up, depending on your application and setup's needs.

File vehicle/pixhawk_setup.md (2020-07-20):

# Configuring the Pixhawk

## First Time Firmware Flash

Depending on where you purchased the Pixhawk from, it is most likely the case that your Pixhawk does not have the correct firmware version flashed on it straight out of the box. The firmware can only be reflashed when connected directly to a PC over USB, so this process will first require us to temporarily disconnect the Pixhawk from the Jetson Nano. Once that is done, the following steps and photos describe how to flash the correct firmware to the Pixhawk.

1. First connect the groundstation PC directly to the Pixhawk via USB micro port
2. Open QGroundControl and wait for it to detect the Pixhawk
3. Click on the `Firmware` tab on the left

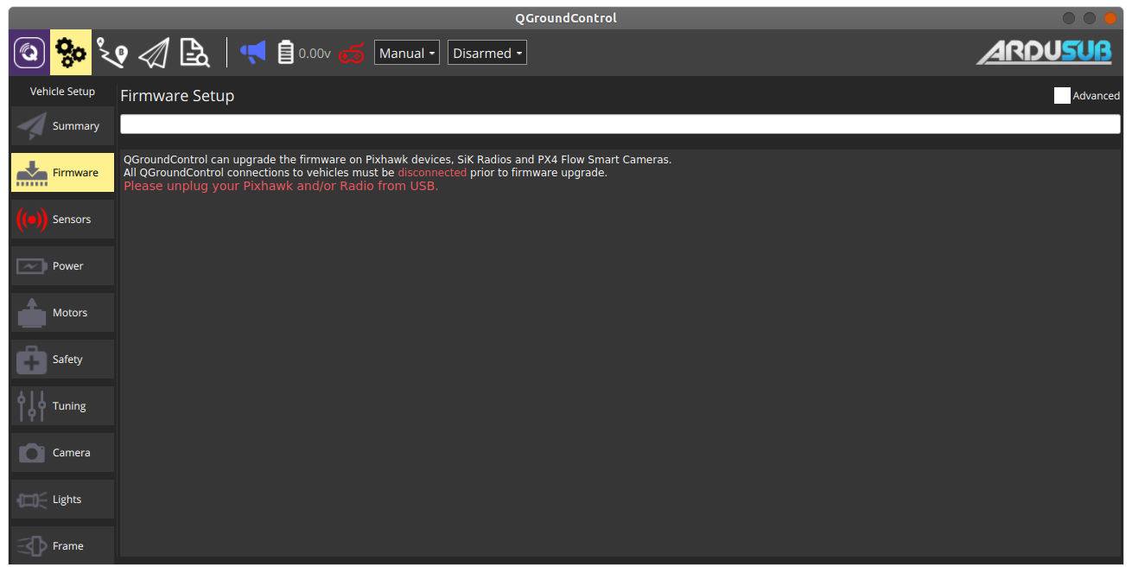
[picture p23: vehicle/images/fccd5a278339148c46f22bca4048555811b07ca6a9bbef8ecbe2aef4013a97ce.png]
  

4. Follow the instructions for flashing new firmware and unplug the Pixhawk, then plug it back in
5. Select the following settings in the box on the right:
   - Ardupilot
   - ChibiOS
   - Rover
   - Pixhawk1 - 4.0.0

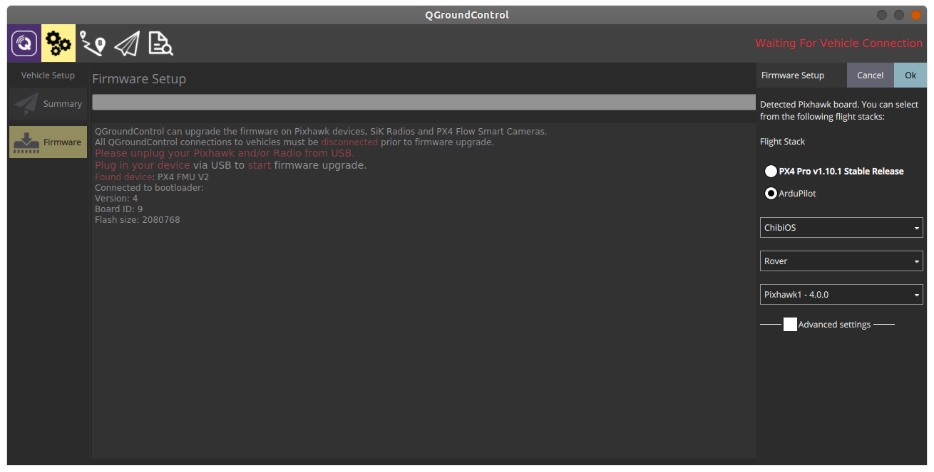
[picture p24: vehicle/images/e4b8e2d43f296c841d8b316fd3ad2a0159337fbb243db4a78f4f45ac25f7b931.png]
  

6. Click Ok to begin the firmware flash process
7. Once the flashing process is complete, the Pixhawk will reboot and QGroundControl will detect it again once it completes the reboot process

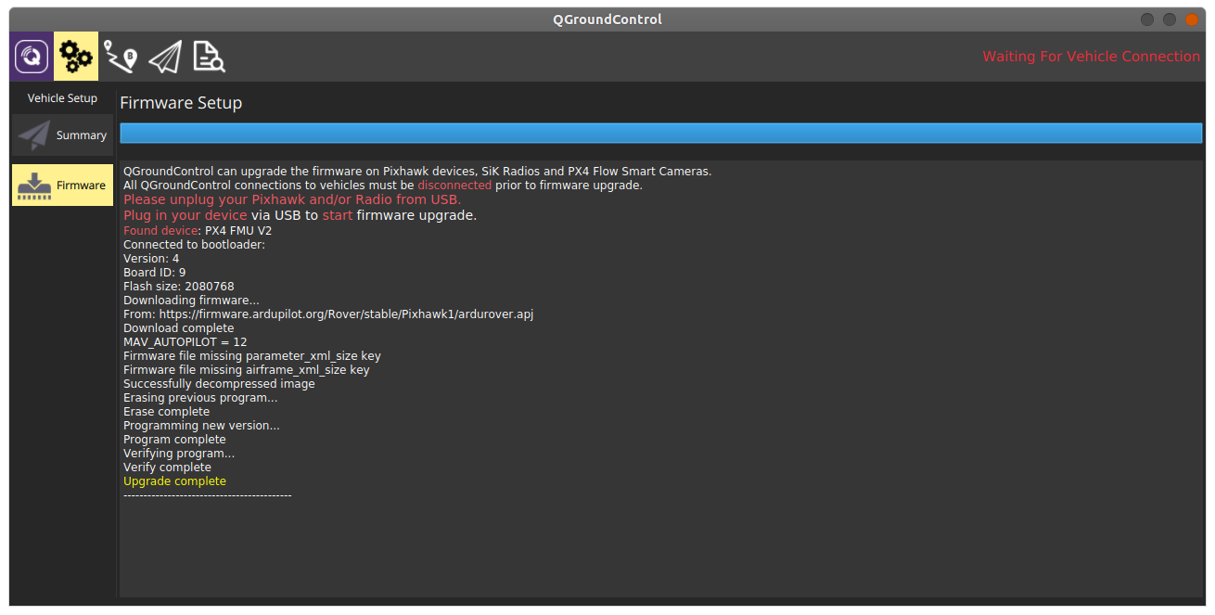
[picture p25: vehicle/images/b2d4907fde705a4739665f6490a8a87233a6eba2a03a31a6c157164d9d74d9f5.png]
  

8. Now that the firmware has been upgraded, you can disconnect the Pixhawk from your groundstation PC and reconnect the Pixhawk to the Jetson Nano.

### System Bring-up

Now that the Pixhawk has the correct firmware and is reconnected to the Jetson Nano, you will need to close the electrical box back up and finish any hardware configurations for your vehicle such that it is ready for flight.

Once all hardware preparations are complete, we are ready to power on the vehicle and make some final software configurations in QGroundControl.

Turn your entire system on, open QGroundControl and make sure you have a connection for the following steps.

```
NOTE: Many of the steps to follow involve rebooting the Pixhawk after making changes. The simplest way to do this with the vehicle fully assembled is to disconnect and reconnect the battery. Please pay attention to all prompts within QGroundControl to reboot after performing certain configurations/calibrations.
```

## Initial Parameter Flash

We will start by uploading a pre-configured baseline parameter file that will get most things working out of the box, provided the motor and pixhawk configuration matches the hardware reference provided in this project. To upload this file:

1. In QGroundControl on the left menu, click the `Parameters` tab
2. In the top right, click the `Tools` button
3. Select `Load from file`
4. Within this git repo, navigate to and select the file: `groundstation/config/asv_initial_params.params`
5. After the file has been successfully uploaded, power cycle the vehicle.

```
NOTE: The safety configurations in this included param file are fairly lax, in terms of aspects like how good of a GPS fix the vehicle needs before allowing a mission to begin and some pre-flight checks that restrict when the vehicle can arm or disarm. If you would like to be more cautious, it is worth reading the Ardurover and QGroundControl docs and reviewing any parameters relating to arming and safety before operating the vehicle in the field.
```

## Frame Configuration

The vehicle frame is selected in the `Frame` tab of the `Vehicle Setup` page. Choose the `Boat` frame.

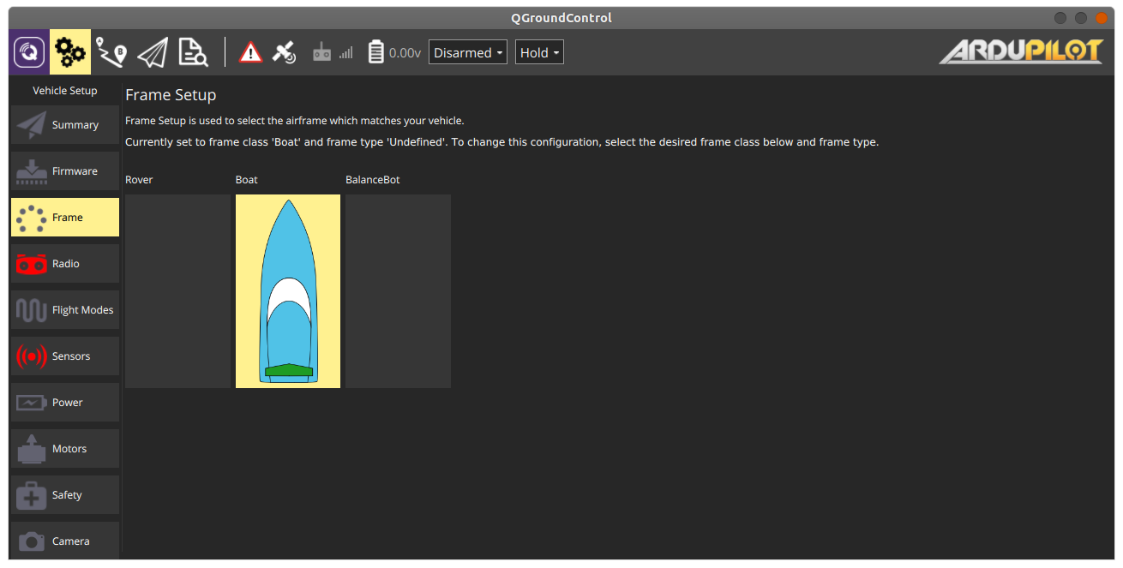
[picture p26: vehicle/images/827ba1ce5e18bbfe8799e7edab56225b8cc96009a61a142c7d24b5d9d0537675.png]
  

## Sensor Calibration

First, depending on how you physically orient the pixhawk, you will need to adjust the autopilot orientation.

1. Go to `Settings`in QGC and select the `Sensors` tab on the left.
2. Choose the appropriate autopilot orientation in the dropdown box:
   - *None* if the Pixhawk's arrow is pointing in the forward direction of travel of your vehicle
   - *YawX* if it is rotated about the Z-axis. You will need to determine the amount (X).

Next, you will need to walk through the calibration process for your sensors:

1. Click on `Accelerometers` and follow the instructions
2. Click on `Compass` and follow the instructions

Finally, you will need to configure the Power parameters, by clicking on the `Power` tab.

1. In the `Battery monitor` field, select `Analog Voltage and Current`
2. The `Battery capacity` field will depend on your battery. If using the BlueRobotics 18Ah battery, set this to 18000 mAh
3. Leave `Minimum arming voltage` set to 0.0
4. In the `Power sensor` field, select `Blue Robotics Power Sense Module R2`

## Further reading

The scope of this project does not currently cover all of the various topics relating to QGroundControl or the Pixhawk/Ardurover configuration, nor does it provide any detailed instruction on how to use these pieces of software. In particular, if you have deviated from the hardware configuration or vehicle topology specified within this tutorial's docs, you may need to further customize the Pixhawk parameters. For further information or more detailed information and instructions for each project, please see the following links:

### ArduRover Docs

<https://ardupilot.org/rover/index.html>

### QGroundControl & Mavlink Docs

<https://www.dronecode.org/documentation/>

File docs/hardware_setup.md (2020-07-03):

# Hardware Setup

# Pre-reqs
## Tools
- Drill + various drill bits (see drawings)
- Deburring tool (to clean up drill holes)
- Screwdriver set (phillips, slotted, hex)
- Crescent wrench (expands to at least 32mm)
- Needle nose pliers
- Scissors or flush cutters

## Parts
Refer to the Bill of Materials (BOM) for the list of parts
### Not on Bill of Materials
- Upper Plate - This part can be laser cut out of 3mm thick material.
- Power Mounting Block - This part can be 3D printed
- Double sided tape (to secure Pixhawk)
- Grease (for o-rings)
- USB 3.0 SSD (for storing data)

# Assembly

## General Assembly Notes
- Make sure to lubricate all o-rings before installation
- M2.5x22mm screws (x4) are only used to attach the fan to the Jetson Nano

## Drill Enclosure
Refer to the drawing PTS-25340-C With Holes for the location the holes should be drilled, as well as the hole diameter. The hole callouts are for clearance holes for parts to fit through. This means the sizes are less common. You can use a drill that is +/- 0.2mm without issue. Also, while all dimensions are metric, sometimes a standard drill bit will be a close match.

## Drill Bottom Plate
Refer to the drawing PTX-25340-P With Holes for the location the holes should be drilled, as well as the hole diameter. The hole callouts are for clearance holes for parts to fit through. This means the sizes are less common. You can use a drill that is +/- 0.2mm without issue. Also, while all dimensions are metric, sometimes a standard drill bit will be a close match.

There are 3 sets of holes for the Eurostyle Terminal Block. This is to allow for some adjustment depending on wire length.

## Battery Tube Assembly
[Follow the Blue Robotics Guide](https://bluerobotics.com/learn/watertight-enclosure-assembly-guide/)

## Electrical Wiring
Follow the System Diagram and Electrical Connections diagrams.

## Final Assembly
### Enclosure Assembly






### Plates Assembly







### Final Assembly Pictures
images
images



## Other Notes
- The two blank penetrators are there for accessories that can be connected to the system.
- The antenna (RP-SMA) connectors on the side of the box can be replaced with cables and different antennas, depending on your use case.
- GPS should have clear view of the sky.
- Keep out of direct sunlight when powered on.

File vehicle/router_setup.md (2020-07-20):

# Router Setup

In our vehicle design, we have chosen to use a separate single-board computer to act as an independent WiFi router through which all LAN communication will occur. While it is possible to plug a USB WiFi adapter into the Jetson Nano and have the Nano act as an Access Point, there are some potential downsides. As a rationale for using the Rambutan:

  - USB WiFi dongle solutions vary greatly in driver quality, stability, and performance. The Rambutan is a solid, reliable solution that has been used in commercial products.
  - By having an independent router handle WiFi connectivity, you can reduce the amount of configuration changes and customizations needed on the Nano, also avoiding the chance of unintentionally misconfiguring the network in the future.
  - The Rambutan features decent transmit power, support for MIMO, and support for 5GHz, aiding in improved performance and flexibility when operating in crowded 2.4GHz airspace.
  - It also has excellent WiFi drivers, coming from the OpenWRT dev efforts (the OS that the Rambutan runs).
  - More advanced network topologies can benefit from the additional flexibility and capabilities provided by having an internal router.
  - It is easy to provide your vehicle with an internet connection while simultaneously having full LAN connectivity by using the Rambutan's ETH0 port which is configured as a gateway. 

# Pre-reqs
First, download the latest OpenWRT image from 8device's Github releases (v2.11 as of the writing of this guide). We will be using this to perform an upgrade of the Rambutan's firmware before beginning configuration:
  - https://github.com/8devices/openwrt-8devices/releases/tag/v2.11-ath71xx
  - You will want the following file:
    - openwrt-8devices-v2.11-ar71xx-nand-rambutan-squashfs-factory.ubi

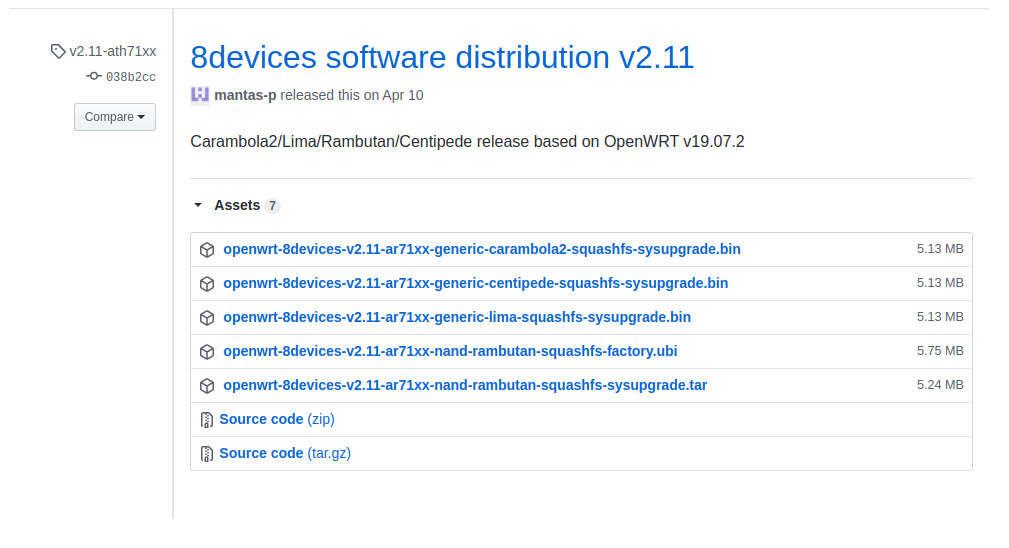
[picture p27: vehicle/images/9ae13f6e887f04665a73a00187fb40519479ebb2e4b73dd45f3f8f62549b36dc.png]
  

# Connecting to the Rambutan
Connect your computer/laptop via ethernet to the ETH1 port on the Rambutan (this is the center ethernet port with the smaller black chip beside it).
```
NOTE: You may need to disconnect from your home WiFi router if it uses the same 192.168.1.0/24 subnet, as it will conflict with the Rambutan, which also defaults to assigning IP addresses on this subnet.
```
  - Navigate in your browser to 192.168.1.1
  - You will be brought to a login page with a banner indicating that no password has been set yet.
  - Click `"Login"`

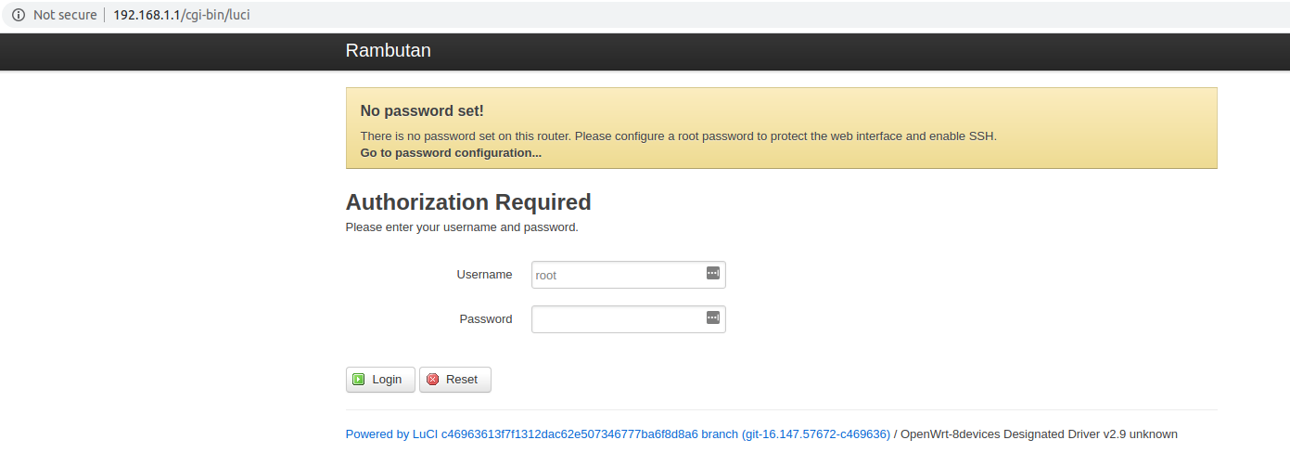
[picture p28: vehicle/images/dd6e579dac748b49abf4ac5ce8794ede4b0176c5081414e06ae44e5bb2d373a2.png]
  

# Setting a Password
When you connect to the Rambutan for the first time, it will not have a password set for the root user. For security reasons, it is a good idea to set one immediately.
  - From the topbar, go to `"System->Administration"`
  - Enter your desired password, click `"Save/Apply"`, and wait for the new settings to be applied.

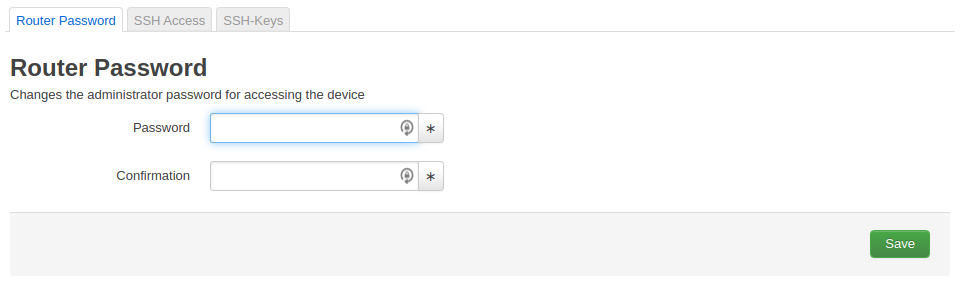
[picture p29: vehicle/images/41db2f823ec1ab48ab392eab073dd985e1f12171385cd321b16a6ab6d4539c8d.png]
  

# Firmware Upgrade
Before proceeding, we will upgrade the firmware for the Rambutan to v2.11, as mentioned earlier.

  - From the topbar, go to `"System->Backup/Flash Firmware"`
  - Under `"Flash new firmware image"`, click `"Choose File"` and select the .ubi file downloaded earlier.
  - Click `"Flash Image"`

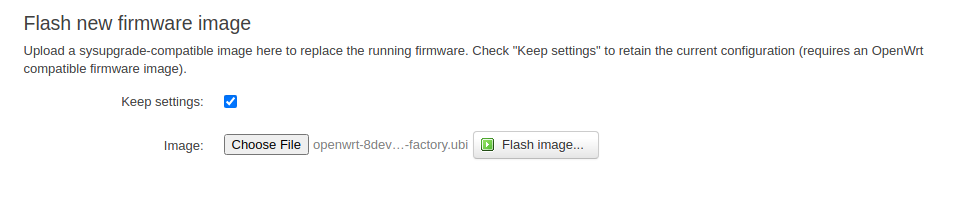
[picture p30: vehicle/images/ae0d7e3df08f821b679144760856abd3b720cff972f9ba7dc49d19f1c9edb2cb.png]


  - You will be taken to a new page to verify the operation to flash the firmware.
  - Click `"Proceed"`

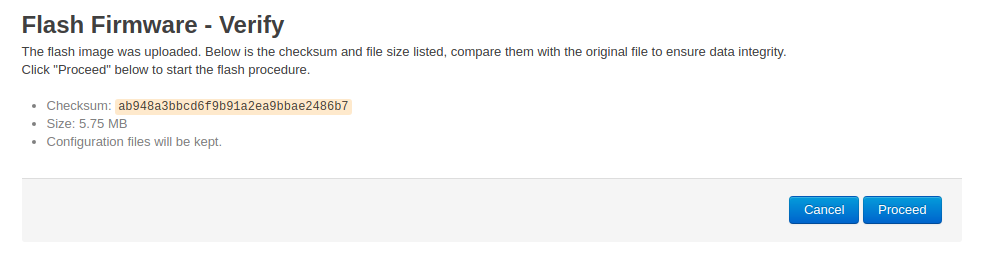
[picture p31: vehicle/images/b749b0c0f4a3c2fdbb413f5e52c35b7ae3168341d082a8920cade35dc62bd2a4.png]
  

  - You will be taken to a page that indicates that the flash is in progress.

  

  - Once it finishes, the page should automatically reload and bring you back to the login screen.
  - Log in once more.

# Changing the LAN Subnet
As mentioned earlier, the default address for the Rambutan is 192.168.1.1 and it assigns IP addresses on the 192.168.1.0/24 subnet. This has a very high likelihood of causing IP address conflicts on your computer when connected to both the Rambutan and your home/office WiFi router simultaneously, as many commodity routers default to using the same subnet. To prevent this, we recommend changing the address and subnet of the Rambutan now.

  - From the topbar, go to `"Network->Interfaces"`
  - Click on `"Edit"` for the LAN Network.

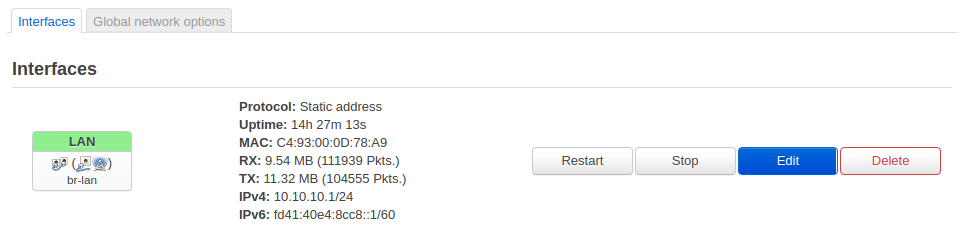
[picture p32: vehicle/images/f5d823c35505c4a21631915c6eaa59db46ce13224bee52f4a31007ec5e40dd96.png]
  

  - Change the value in the IPv4 Address box to 10.10.10.1 (or any LAN address that you are reasonably certain won't conflict with commodity WiFi systems)
  - Click "Save"

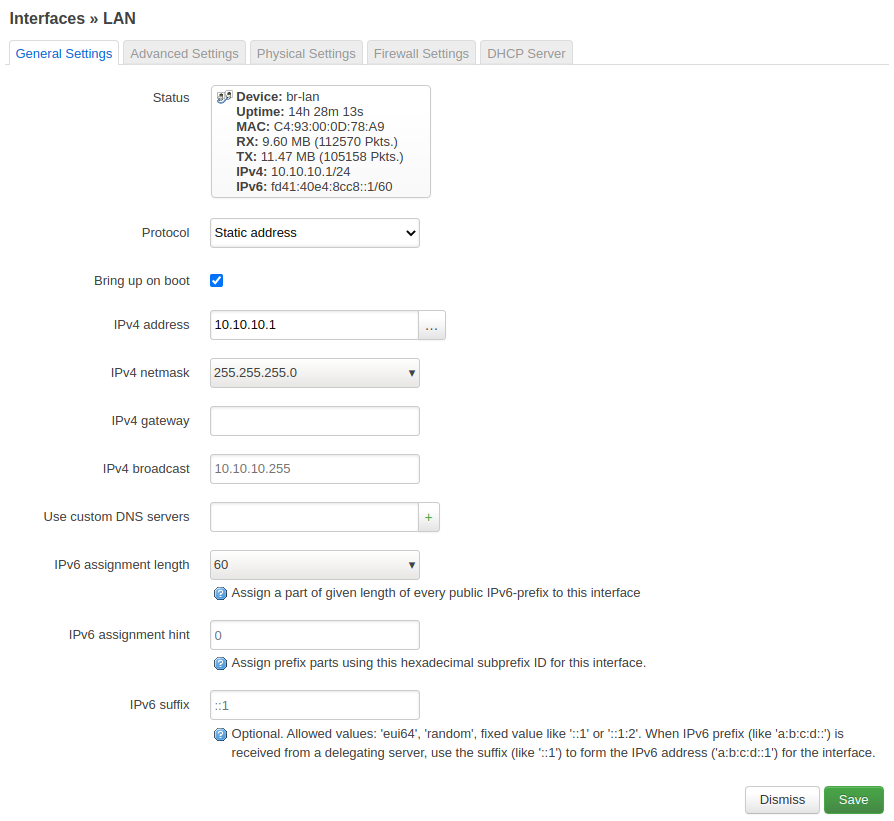
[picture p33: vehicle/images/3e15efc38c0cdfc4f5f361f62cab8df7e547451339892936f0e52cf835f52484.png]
  

  - Click the drop down arrow to the right of "Save and Apply" and click "Apply Unchecked"

  

  - It will apply the settings and try to reconnect, but since the IP is changed, it will not be able to reach the page address.

  

 - Navigate now to 10.10.10.1 (or whichever IP you specified).
 - It will take some time for the router to finish applying the settings and assign you a new IP address.
   - You may need to unplug and replug the ethernet connector to either your computer or the Rambutan to get a new IP Address, or otherwise use the appropriate method within your OS to achieve the same effect.

Now you can reconnect to your personal WiFi/home network while simultaneously staying connected to the Rambutan's local network (effectively, your vehicle's private network).

# Configuring and Enabling WiFi
The last steps are to configure and enable the WiFi access point on the Rambutan, which is disabled by default for security reasons.

  - From the topbar, go to `"Network->Wireless"`

  

  - Click `"Edit"` on the "SSID: Rambutan" interface
  - Under the `"Device Configuration->General Setup"` tab:
    - Set transmit power to 21dBm (or the max allowed by your country's regulations). 
      - You can choose your country on the `"Device Configuration->Advanced Settings"` tab.
    - (Optional) Set the desired operating frequency mode, band, channel, and bandwidth, if desired. We recommend:
      - Mode: N
      - Band 2.4GHz
      - Channel: auto
      - Width: 20MHz

```
NOTE: If you are operating in a dense urban area or generally crowded 2.4GHz airspace, you may want to try using the 5GHz band.
```

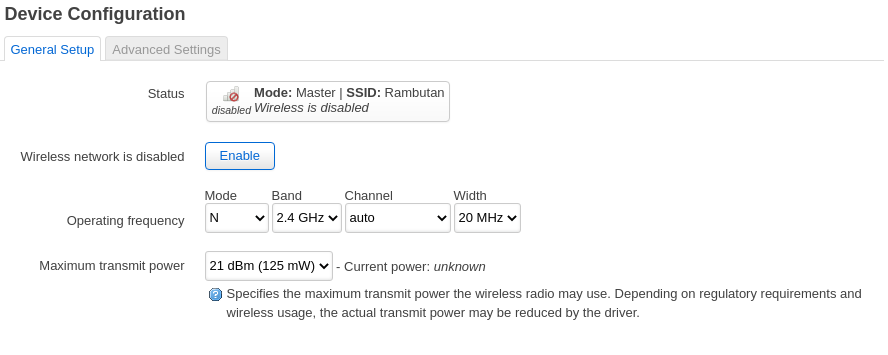
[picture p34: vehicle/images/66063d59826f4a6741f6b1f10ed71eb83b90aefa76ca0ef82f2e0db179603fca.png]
  

  - Under the `"Interface Configuration->General Setup"` tab:
    - (Optional) If desired, you can change the ESSID from Rambutan to anything you desire (your vehicle's name is often a good choice).

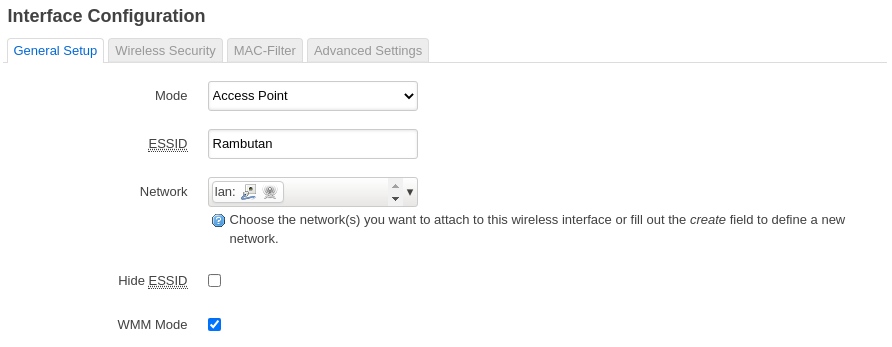
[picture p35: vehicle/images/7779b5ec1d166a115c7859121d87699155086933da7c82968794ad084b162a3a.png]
  

  - (Recommended) Under the `"Interface Configuration->Wireless Security"` tab
    - Set the desired encryption type (such as WPA2-PSK) and key.

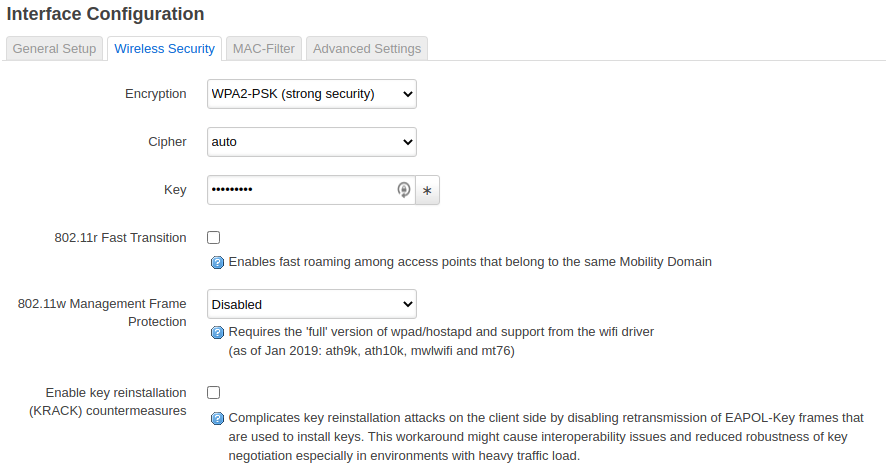
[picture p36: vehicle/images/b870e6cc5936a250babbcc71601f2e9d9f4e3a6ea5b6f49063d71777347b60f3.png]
  

  - Click `"Save"`
  - Click `"Save & Apply"`.
  - The last step is to enable the WiFi interface we just configured. Click `"Enable"` (next to `"Edit"`).
  
Wait for the Access Point to come up. Once ready, you should now be able to connect your laptop and other devices to the Rambutan over WiFi. You can now disconnect the ethernet between your computer and the Rambutan. Any further modifications of settings can be done via WiFi.

# Other Notes
You can find the user guide from the manufacturer here:
  - https://www.8devices.com/wiki/rambutan:userguide

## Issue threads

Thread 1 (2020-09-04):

Missing GPS Cable in BOM

keenanjohnson, 2020-09-04:
I believe the Bill of Materials is missing the Cable to Connect the GPS Module to the Pixhawk.

keenanjohnson, 2020-09-04:
Not sure if anyone is maintaining this project or not, but I'm in the midst of trying to replicate the build.

The BOM only lists one of the MRC0203 cables, but I believe you need two for the GPS and the power module to connect to the pixhawk.

drewjgray, 2020-09-04:
Thanks @keenanjohnson will take a look with @spiderkeys

keenanjohnson, 2020-09-04:
Thanks! Out of curiosity, are you actively working on this project?

I'm interested in the state of the hull / solar panel design since I've actively building one and would rather work together to do that.

keenanjohnson, 2020-09-04:
I sent an email to the contact email listed a while ago but never heard anything.

spiderkeys, 2020-09-04:
Hi @keenanjohnson. The MRC0203 cable is, as you've identified, for the GPS<->Pixhawk connection. The power sense module comes with its own DF13-JST-GH cable, which is why only one is specified in the BOM.

The BOM calls out this particular component from Blue:
https://bluerobotics.com/store/comm-control-power/elec-packages/psm-asm-r2-rp/

If you scroll down and expand "Contents" under the product description, it lists both the module and 1 x 200mm DF13 to JST-GH cable.

drewjgray, 2020-09-07:
We are actively working on this project, but we are not currently manufacturing the hull we designed. If we get enough interest we may go ahead and make them. If we get there, we will definitely let you know!

keenanjohnson, 2020-09-08:
That'd be great! In the meantime, is there any easy hull you would
recommend for testing?

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

Closed 2020-09-07.

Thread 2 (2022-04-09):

Nano setup, vehicle software build.sh file missing

shubham159071, 2022-04-09:
while doing Nano setup, in the vehicle software setup the build.sh file is missing in the src folder of vehicle. on running build.sh file of vehicle folder I am getting error. attaching the sniptes of my issue please help
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

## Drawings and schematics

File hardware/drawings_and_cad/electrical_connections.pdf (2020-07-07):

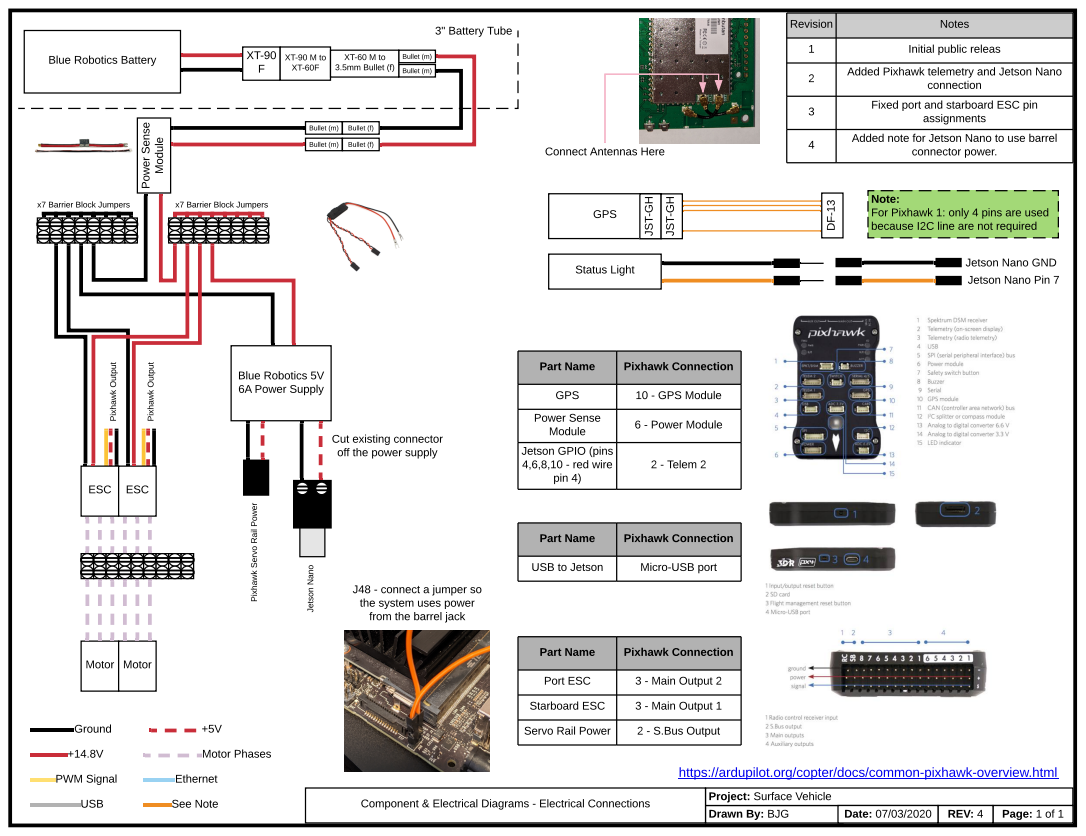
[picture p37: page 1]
Ground; PWM Signal; USB; Ethernet; Motor Phases; See Note; Drawn By: BJG; Component & Electrical Diagrams - Electrical Connections; Date: 07/03/2020; REV: 4; Motor Motor; ESC ESC; Pixhawk Output; x7 Barrier Block Jumpers; Blue Robotics 5V 6A Power Supply; Status Light; Jetson Nano; Blue Robotics Battery; Bullet (m); Bullet (f); XT-60 M to 3.5mm Bullet (f); 3" Battery Tube; GPS

Revision | Notes
1 | Initial public releas
2 | Added Pixhawk telemetry and Jetson Nano connection

3 | Fixed port and starboard ESC pin assignments

Power Sense Module

4 | Added note for Jetson Nano to use barrel connector power.

Connect Antennas Here

Note:
For Pixhawk 1: only 4 pins are used
because I2C line are not required

Jetson Nano GND
Jetson Nano Pin 7

Part Name | Pixhawk Connection

GPS | 10 - GPS Module
Power Sense Module | 6 - Power Module

Cut existing connector
off the power supply

Jetson GPIO (pins 4,6,8,10 - red wire pin 4) | 2 - Telem 2

Pixhawk Servo Rail Power

USB to Jetson | Micro-USB port

J48 - connect a jumper so
the system uses power
from the barrel jack

Port ESC | 3 - Main Output 2
Starboard ESC | 3 - Main Output 1
Servo Rail Power | 2 - S.Bus Output

https://ardupilot.org/copter/docs/common-pixhawk-overview.html
Project: Surface Vehicle

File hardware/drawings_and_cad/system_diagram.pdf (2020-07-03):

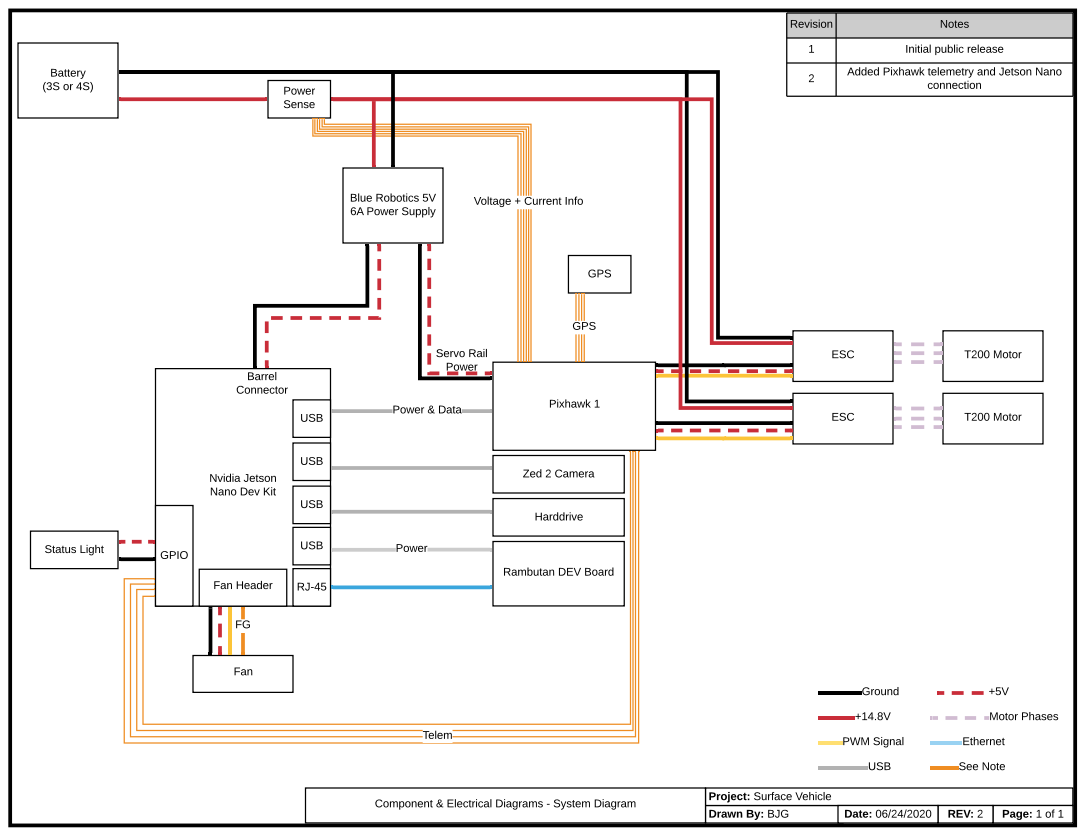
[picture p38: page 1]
Zed 2 Camera; Pixhawk 1; ESC; Status Light; Harddrive; Battery (3S or 4S); GPS; Ground; PWM Signal; USB; Ethernet; GPIO; Blue Robotics 5V 6A Power Supply; T200 Motor; Motor Phases; Power & Data; See Note; Power; Barrel Connector; Servo Rail Power; REV: 2; connection Power Sense; Fan; Fan Header; Date: 06/24/2020; Telem

Revision | Notes
1 | Initial public release
2 | Added Pixhawk telemetry and Jetson Nano

Voltage + Current Info

Nvidia Jetson Nano Dev Kit

Rambutan DEV Board

Component & Electrical Diagrams - System Diagram

Project: Surface Vehicle
Drawn By: BJG

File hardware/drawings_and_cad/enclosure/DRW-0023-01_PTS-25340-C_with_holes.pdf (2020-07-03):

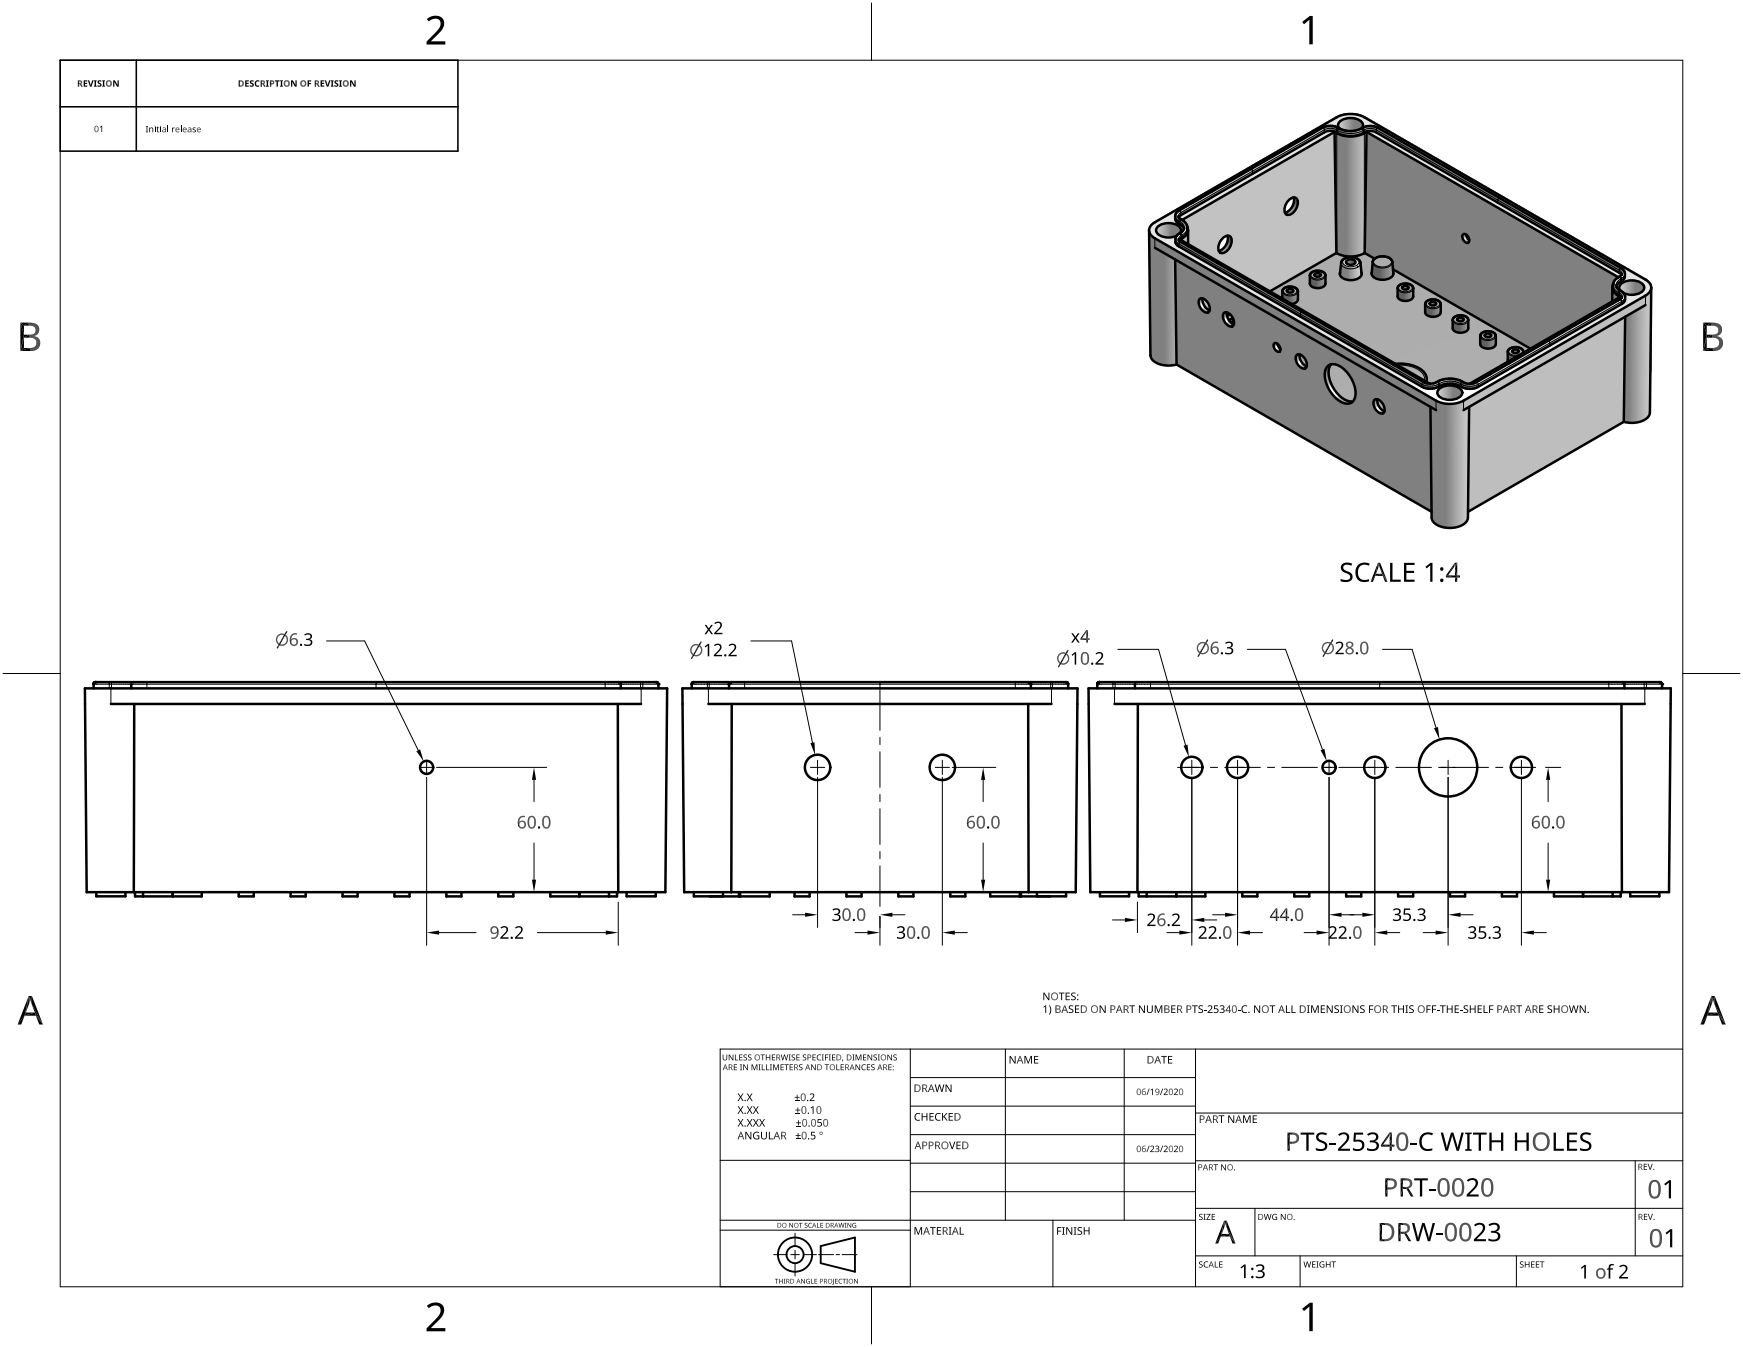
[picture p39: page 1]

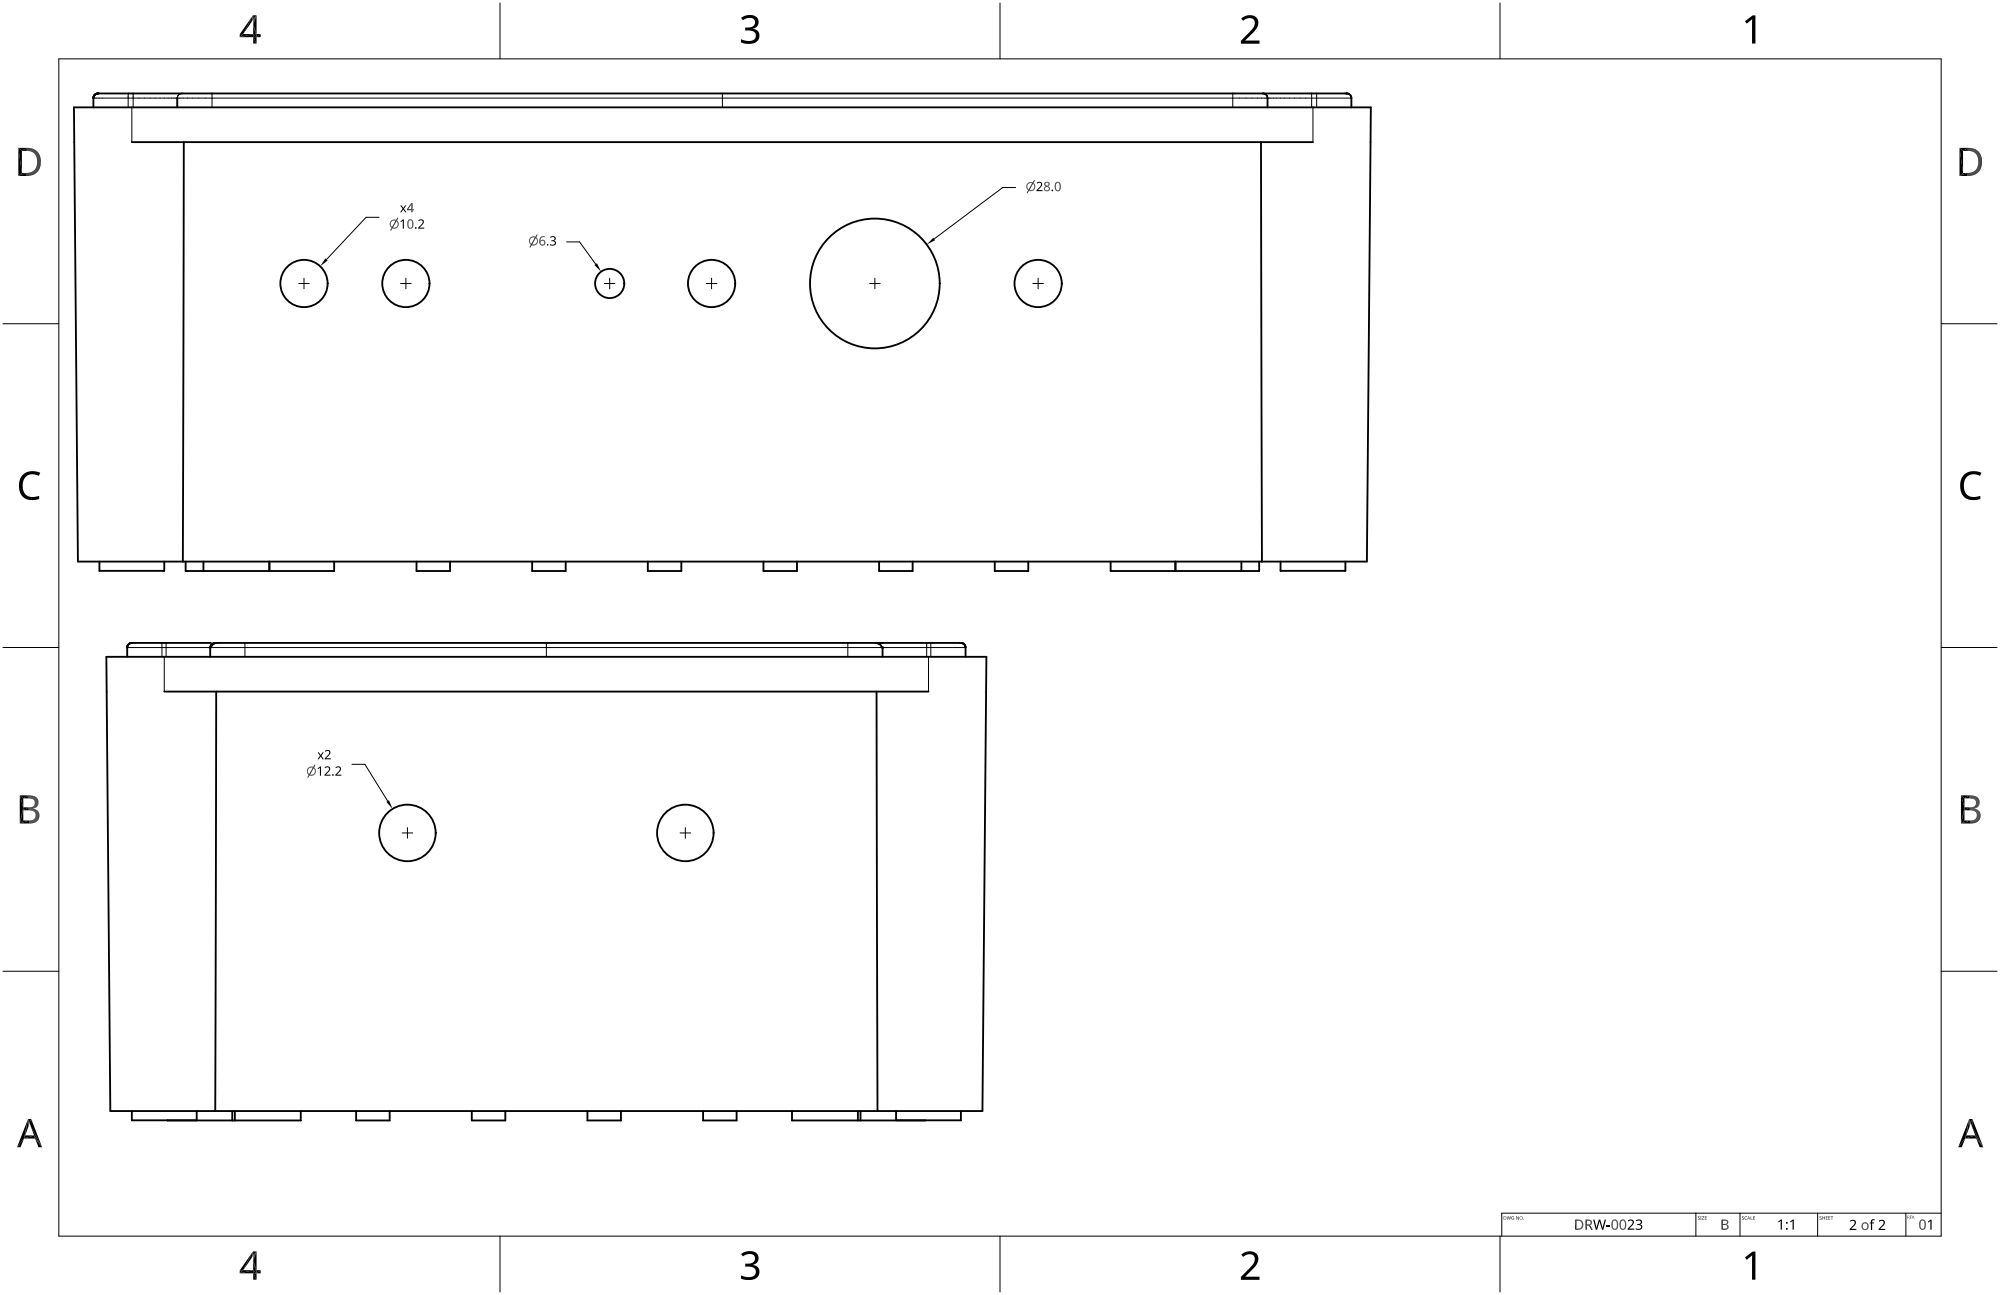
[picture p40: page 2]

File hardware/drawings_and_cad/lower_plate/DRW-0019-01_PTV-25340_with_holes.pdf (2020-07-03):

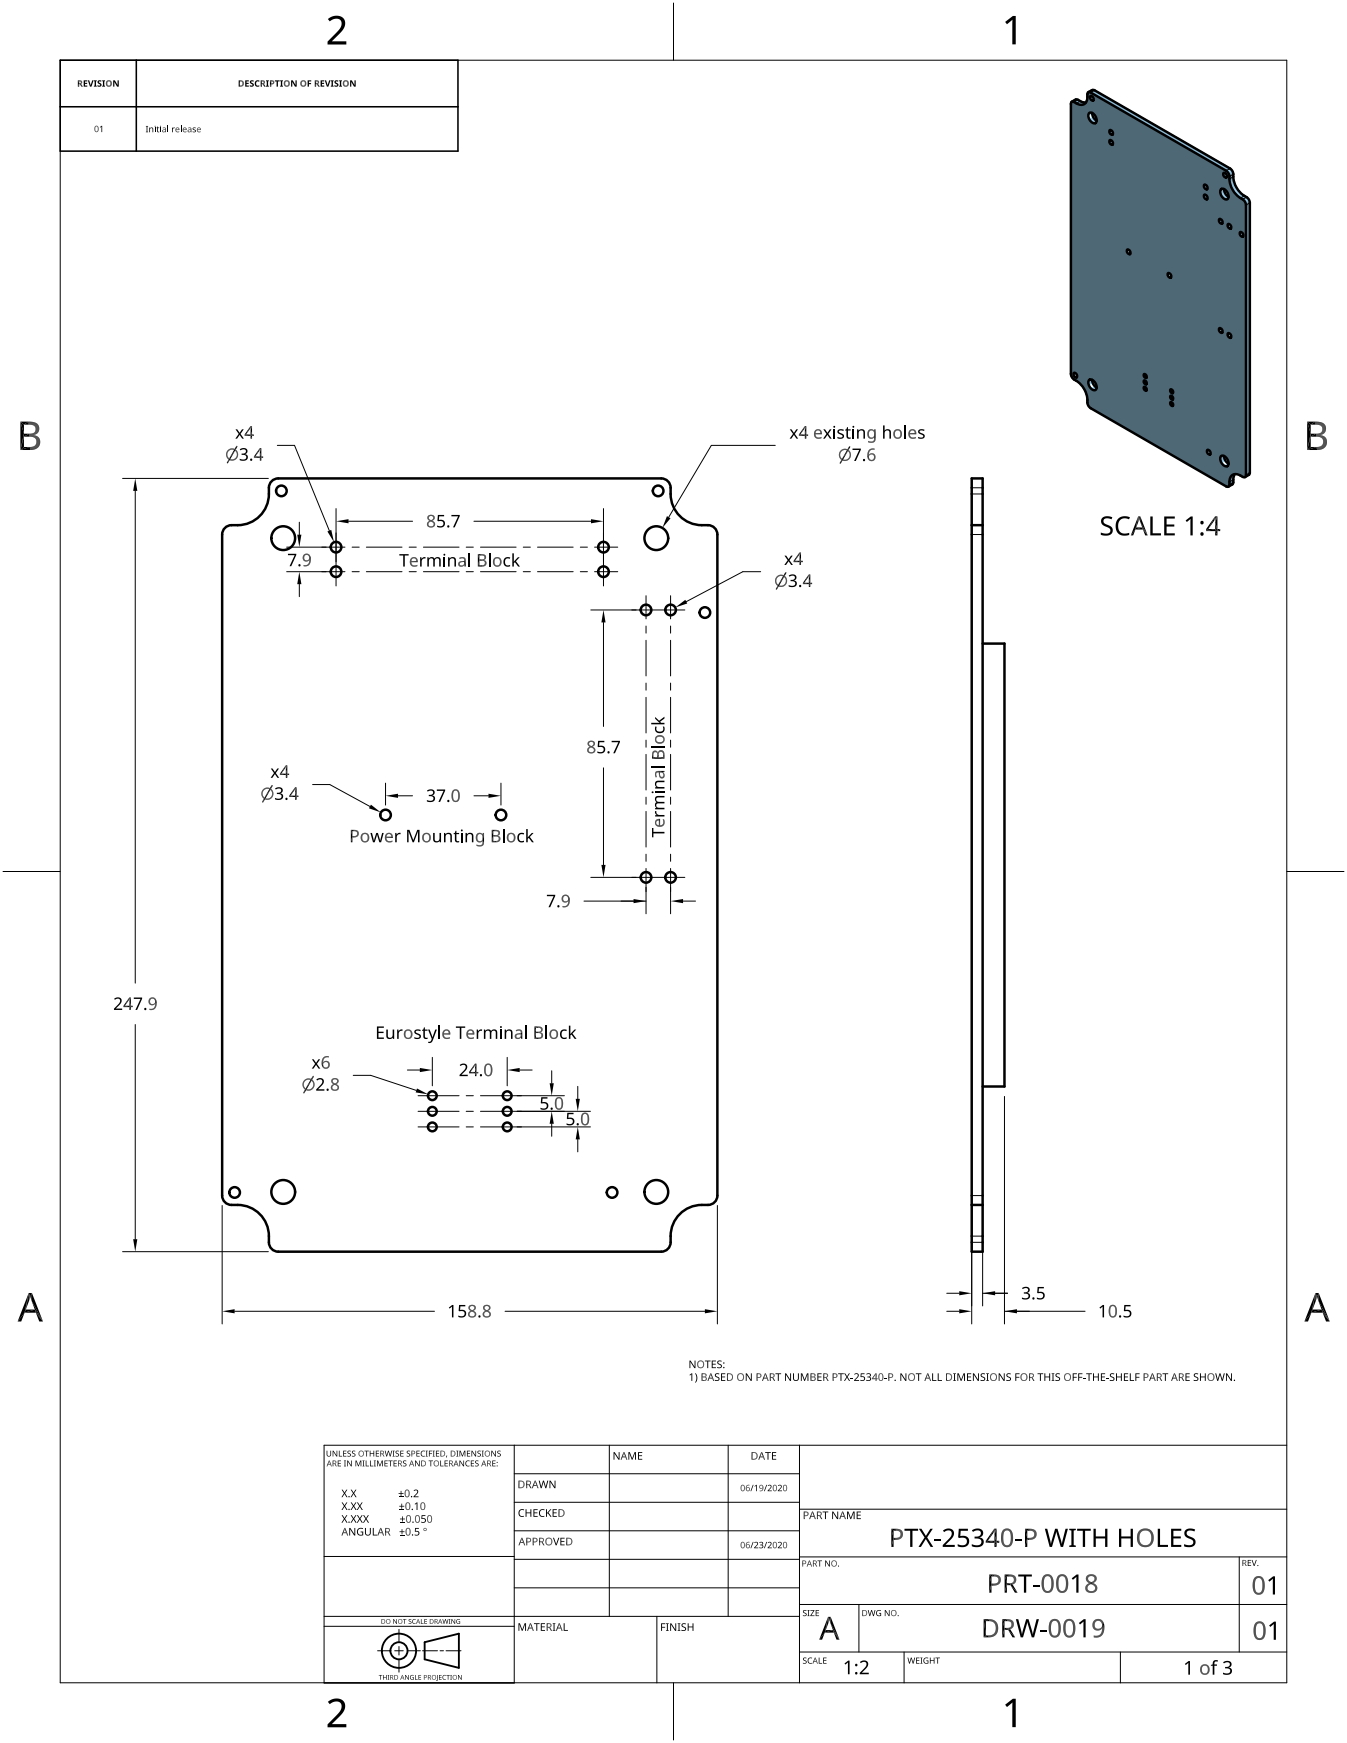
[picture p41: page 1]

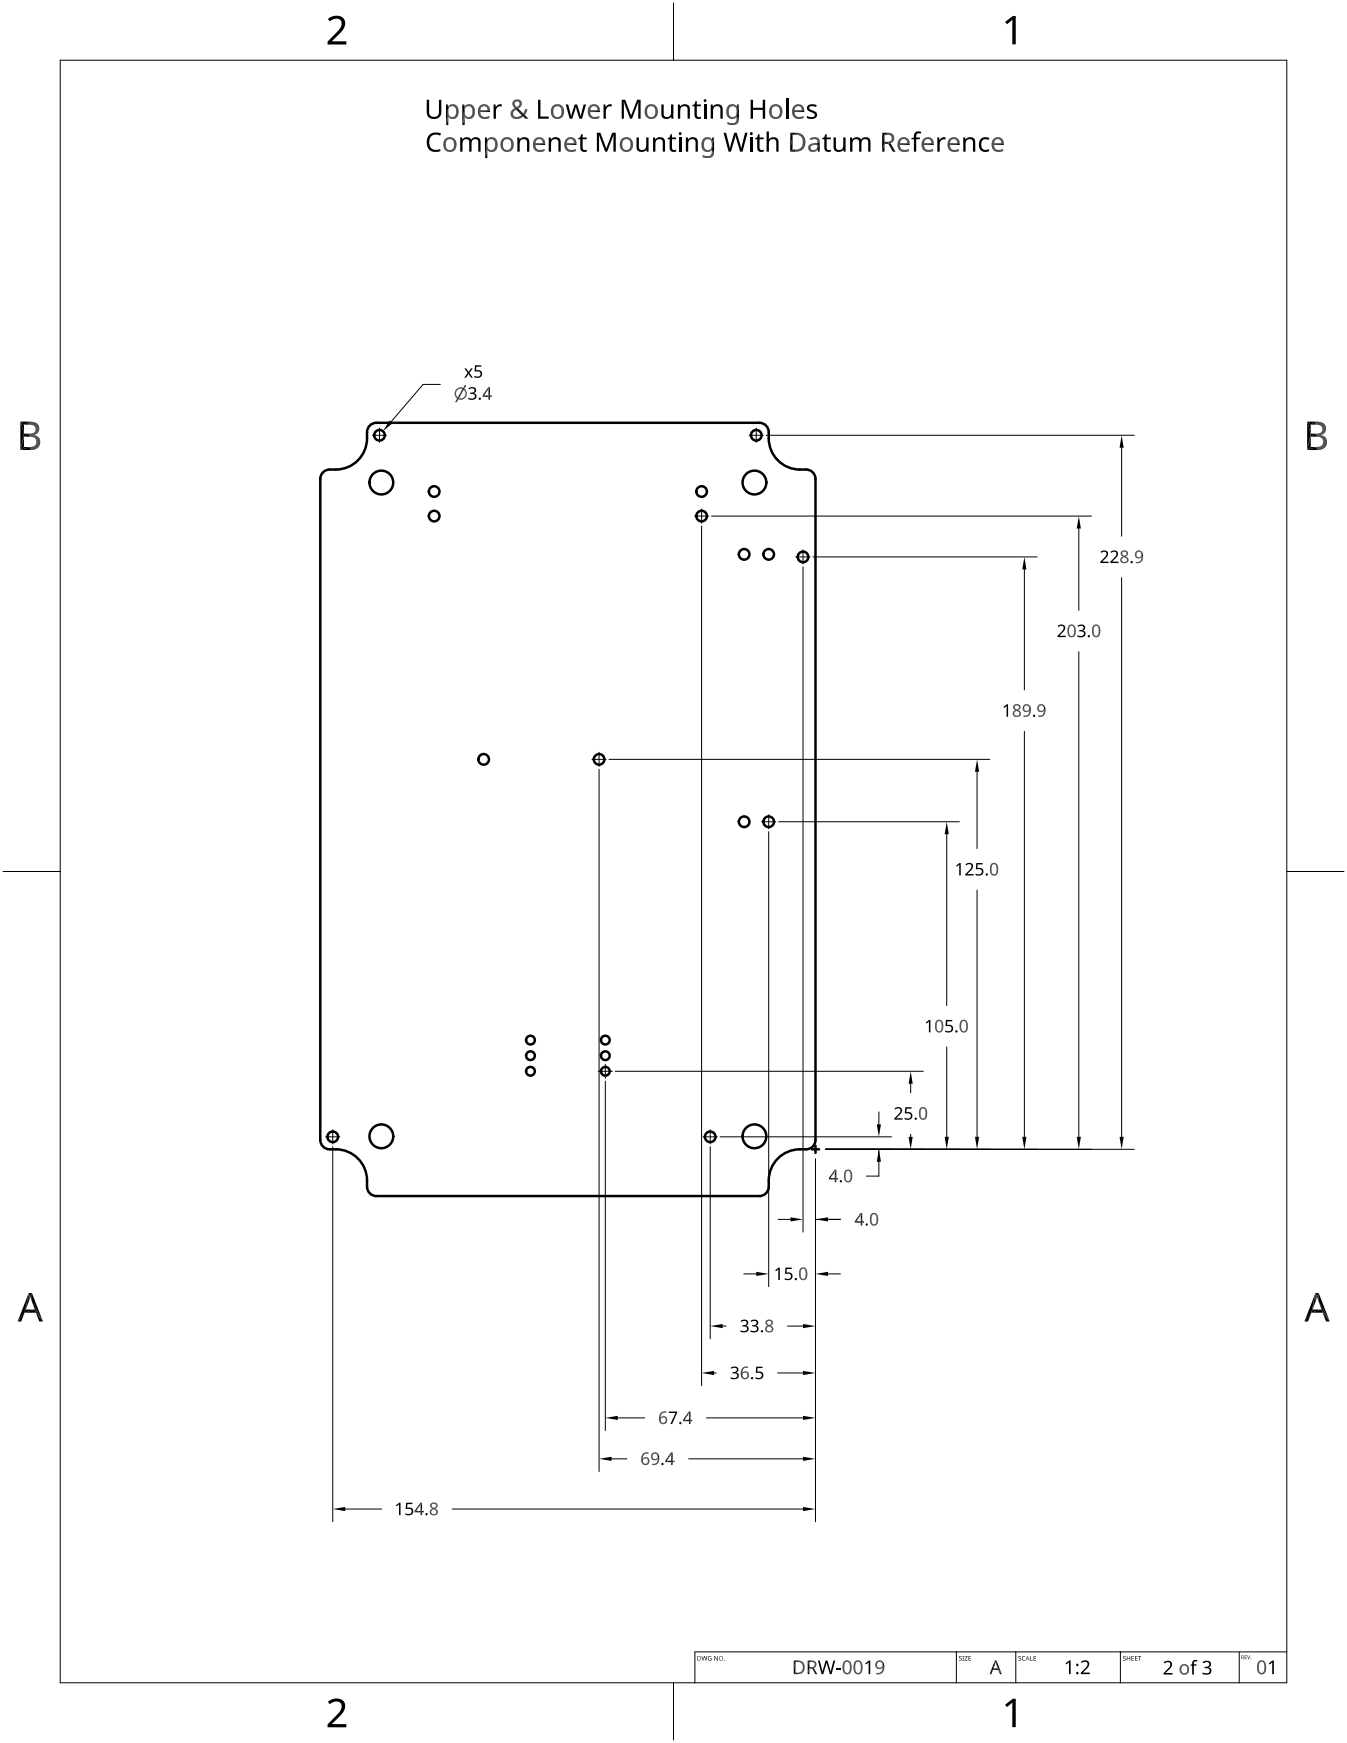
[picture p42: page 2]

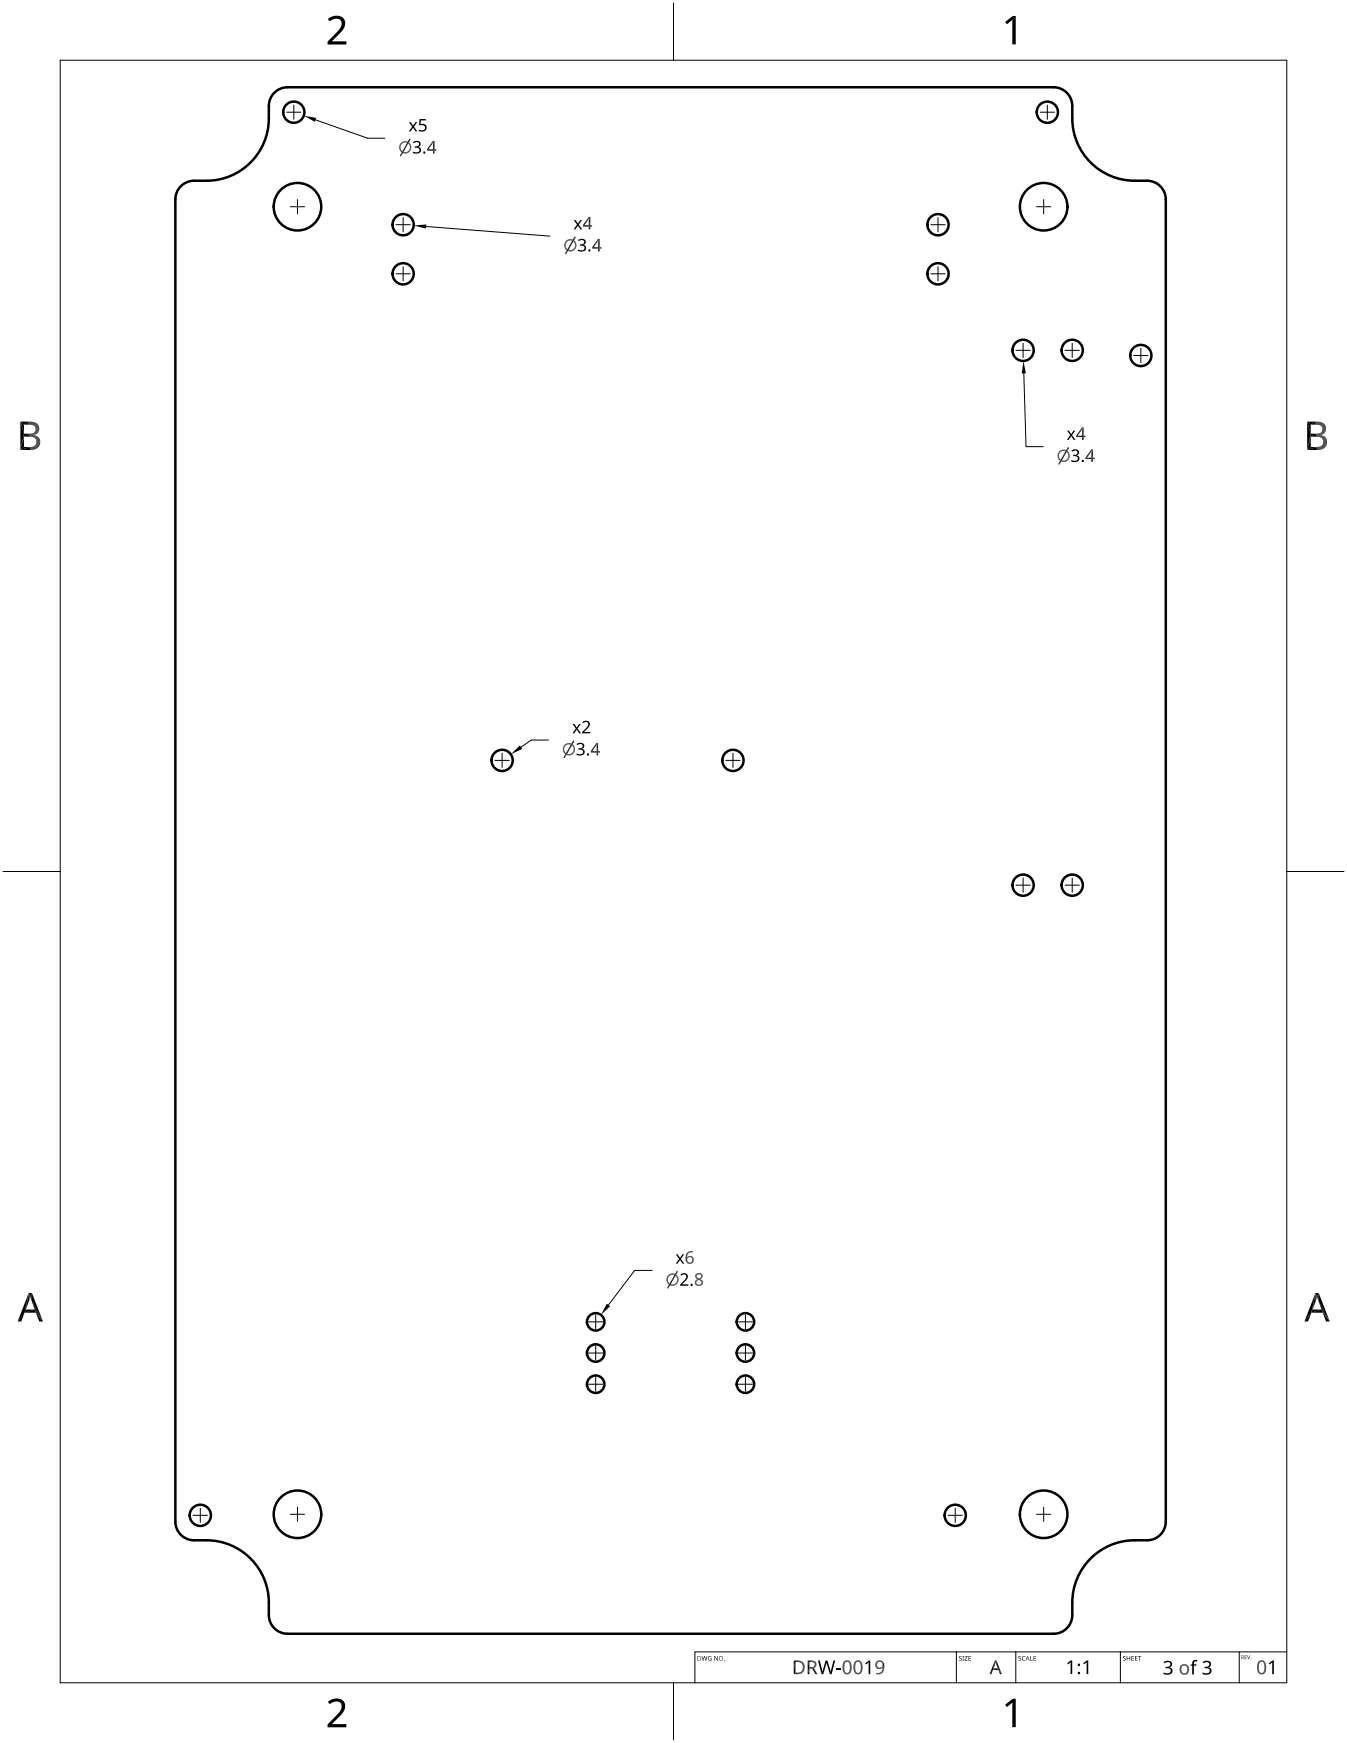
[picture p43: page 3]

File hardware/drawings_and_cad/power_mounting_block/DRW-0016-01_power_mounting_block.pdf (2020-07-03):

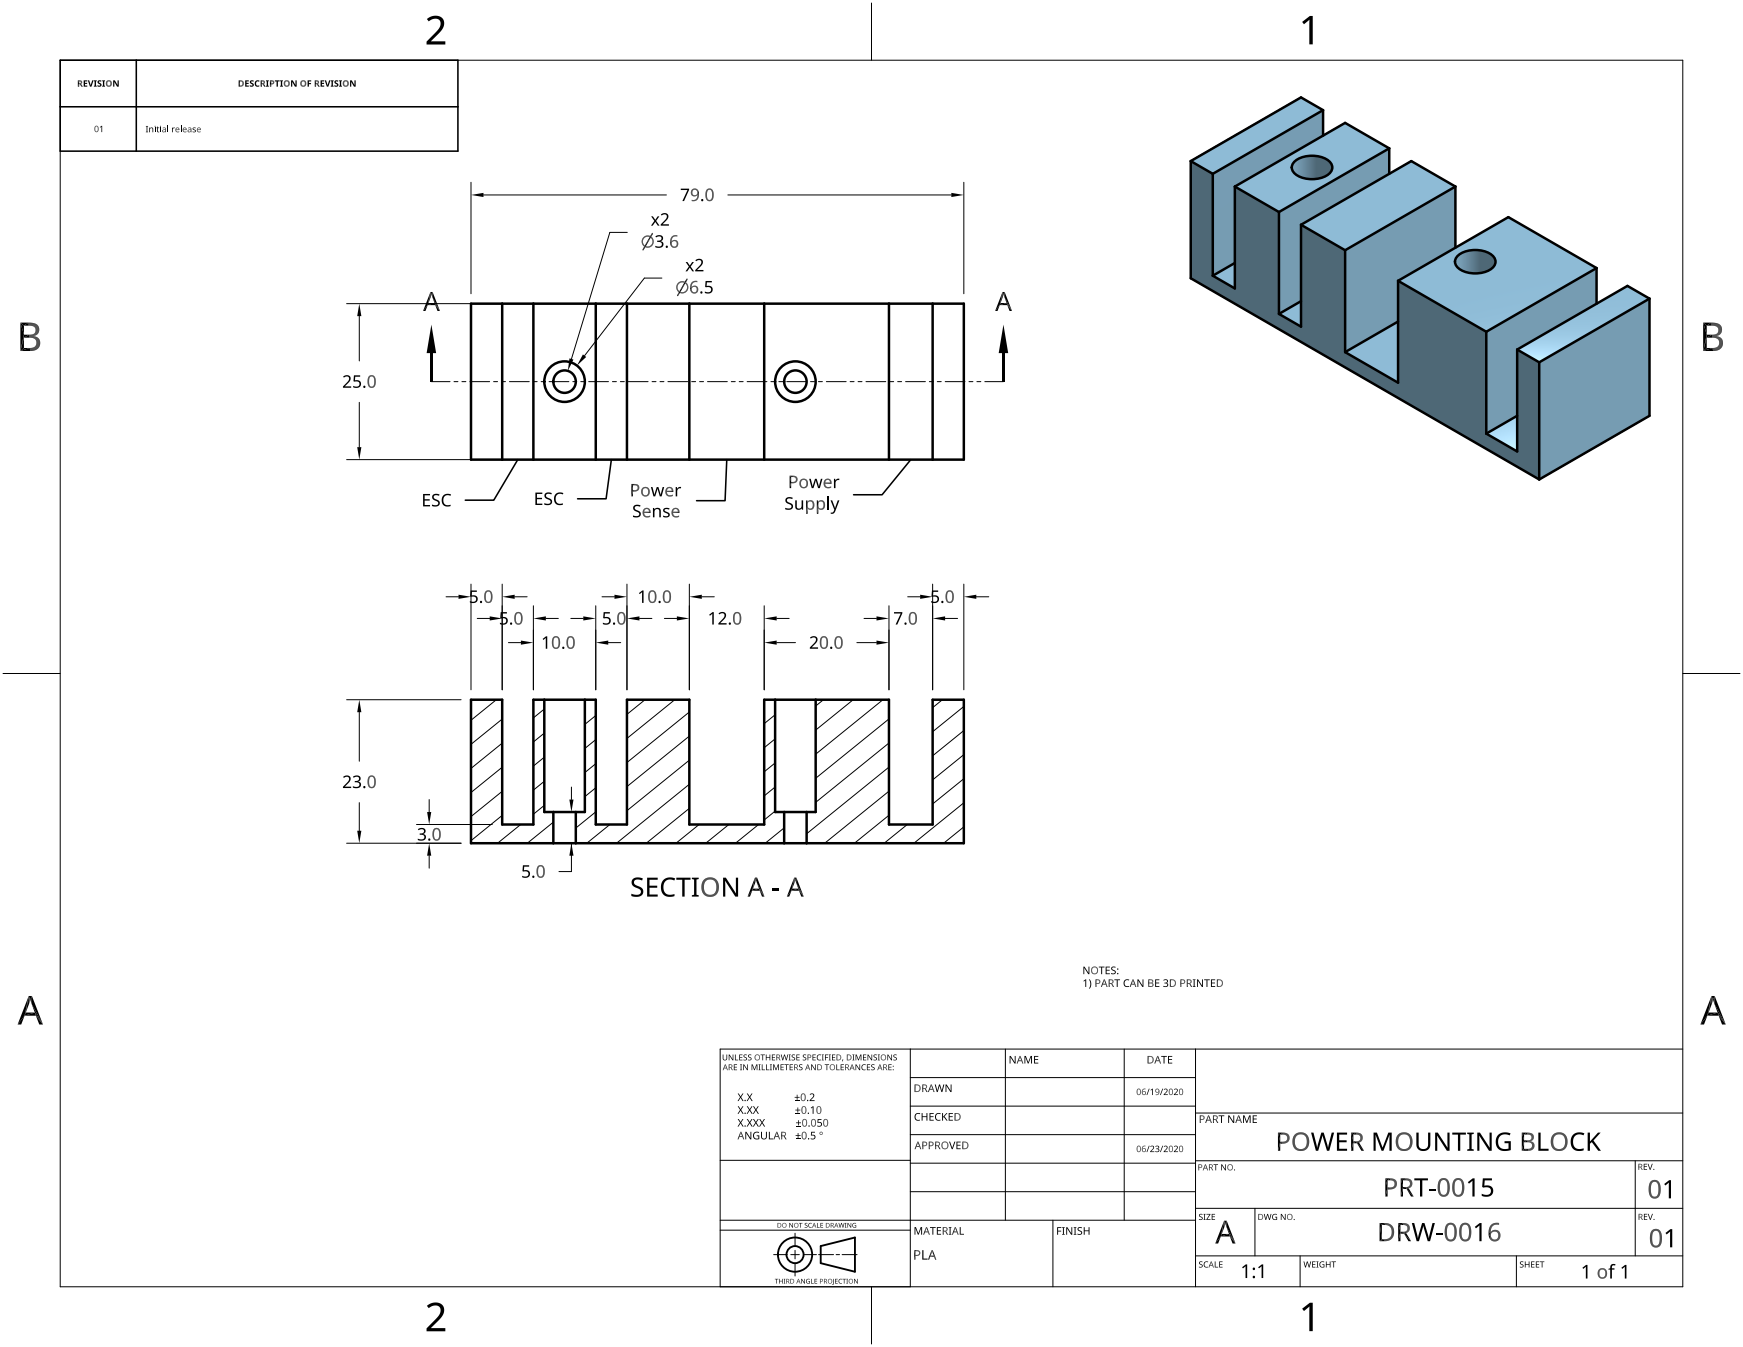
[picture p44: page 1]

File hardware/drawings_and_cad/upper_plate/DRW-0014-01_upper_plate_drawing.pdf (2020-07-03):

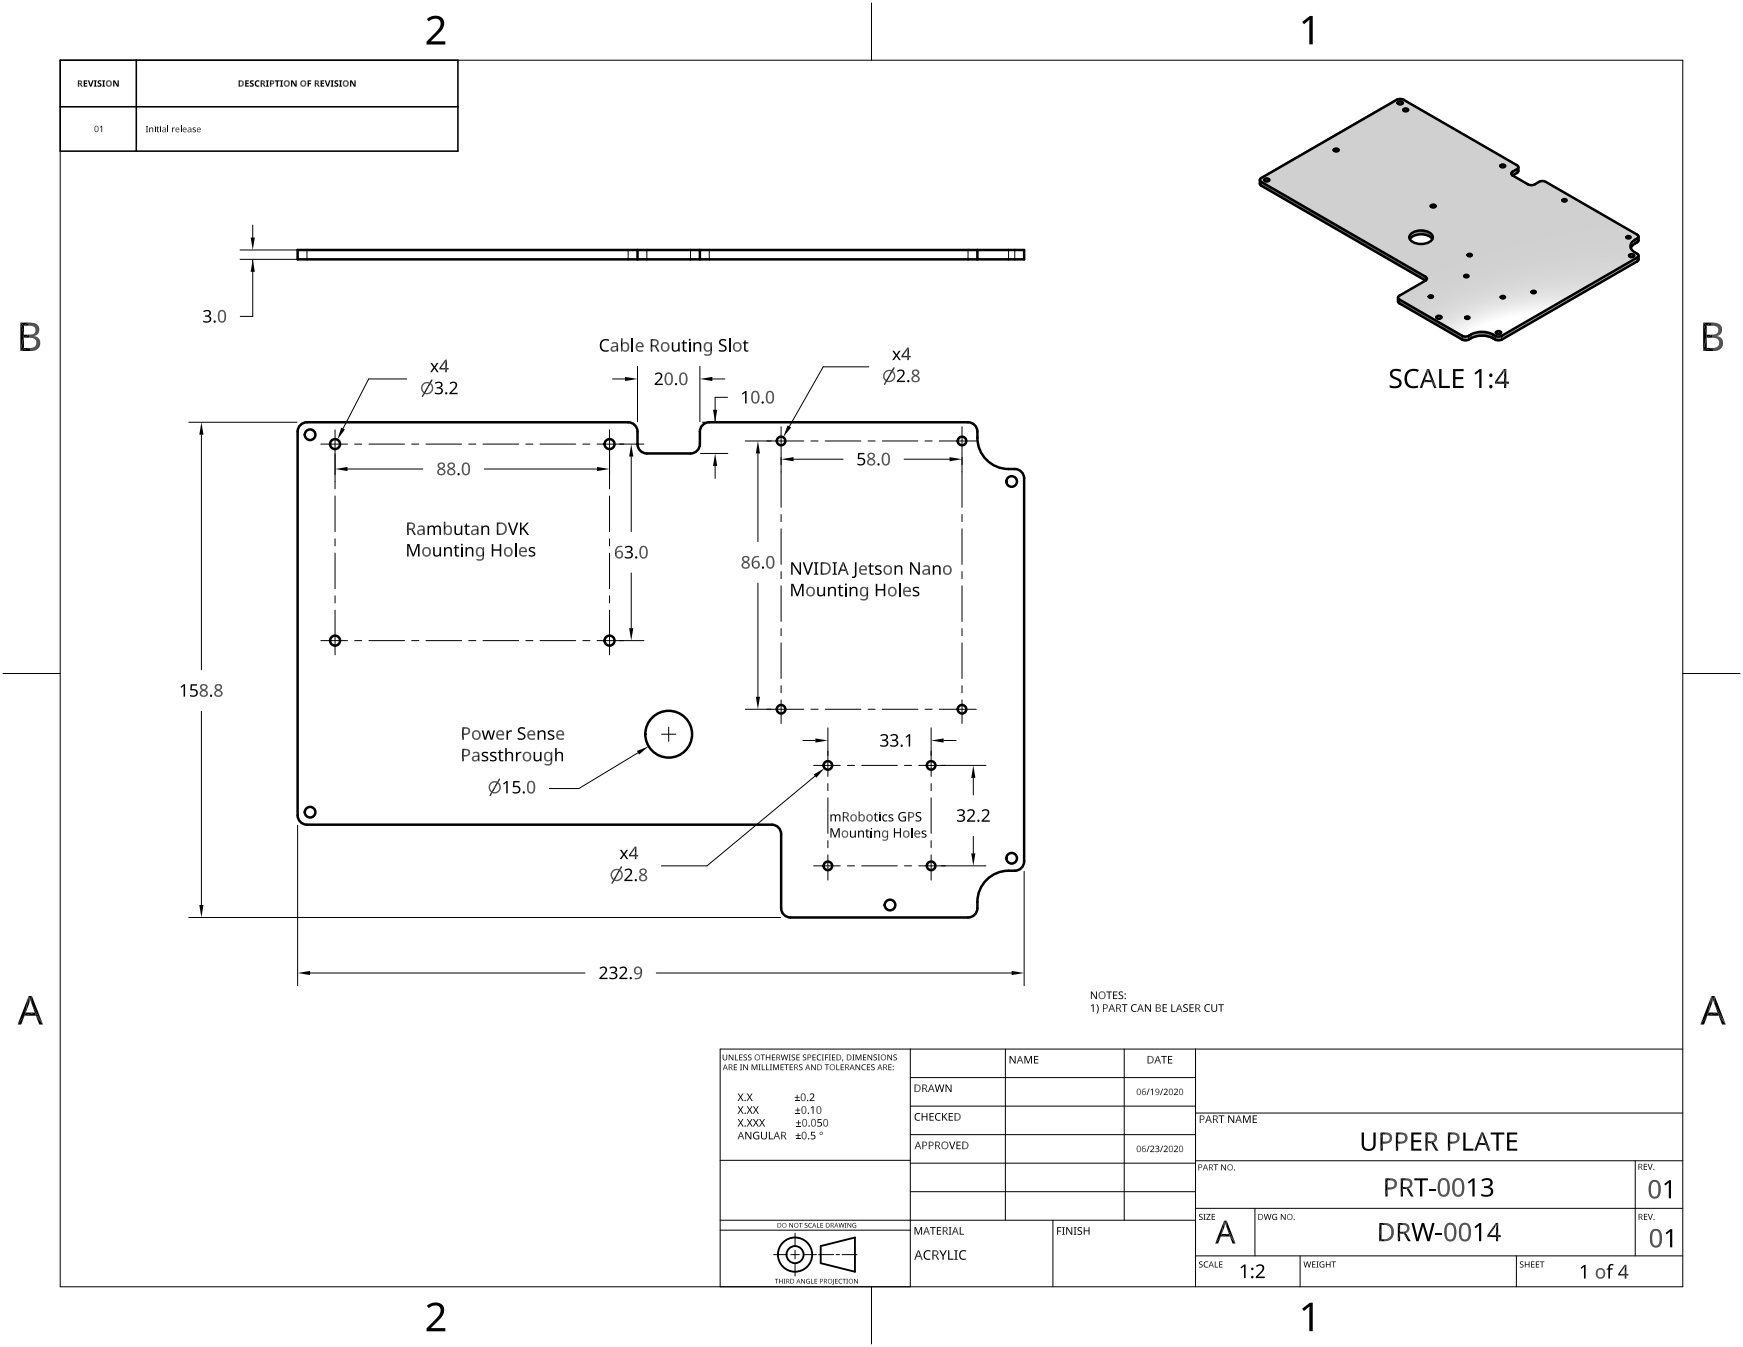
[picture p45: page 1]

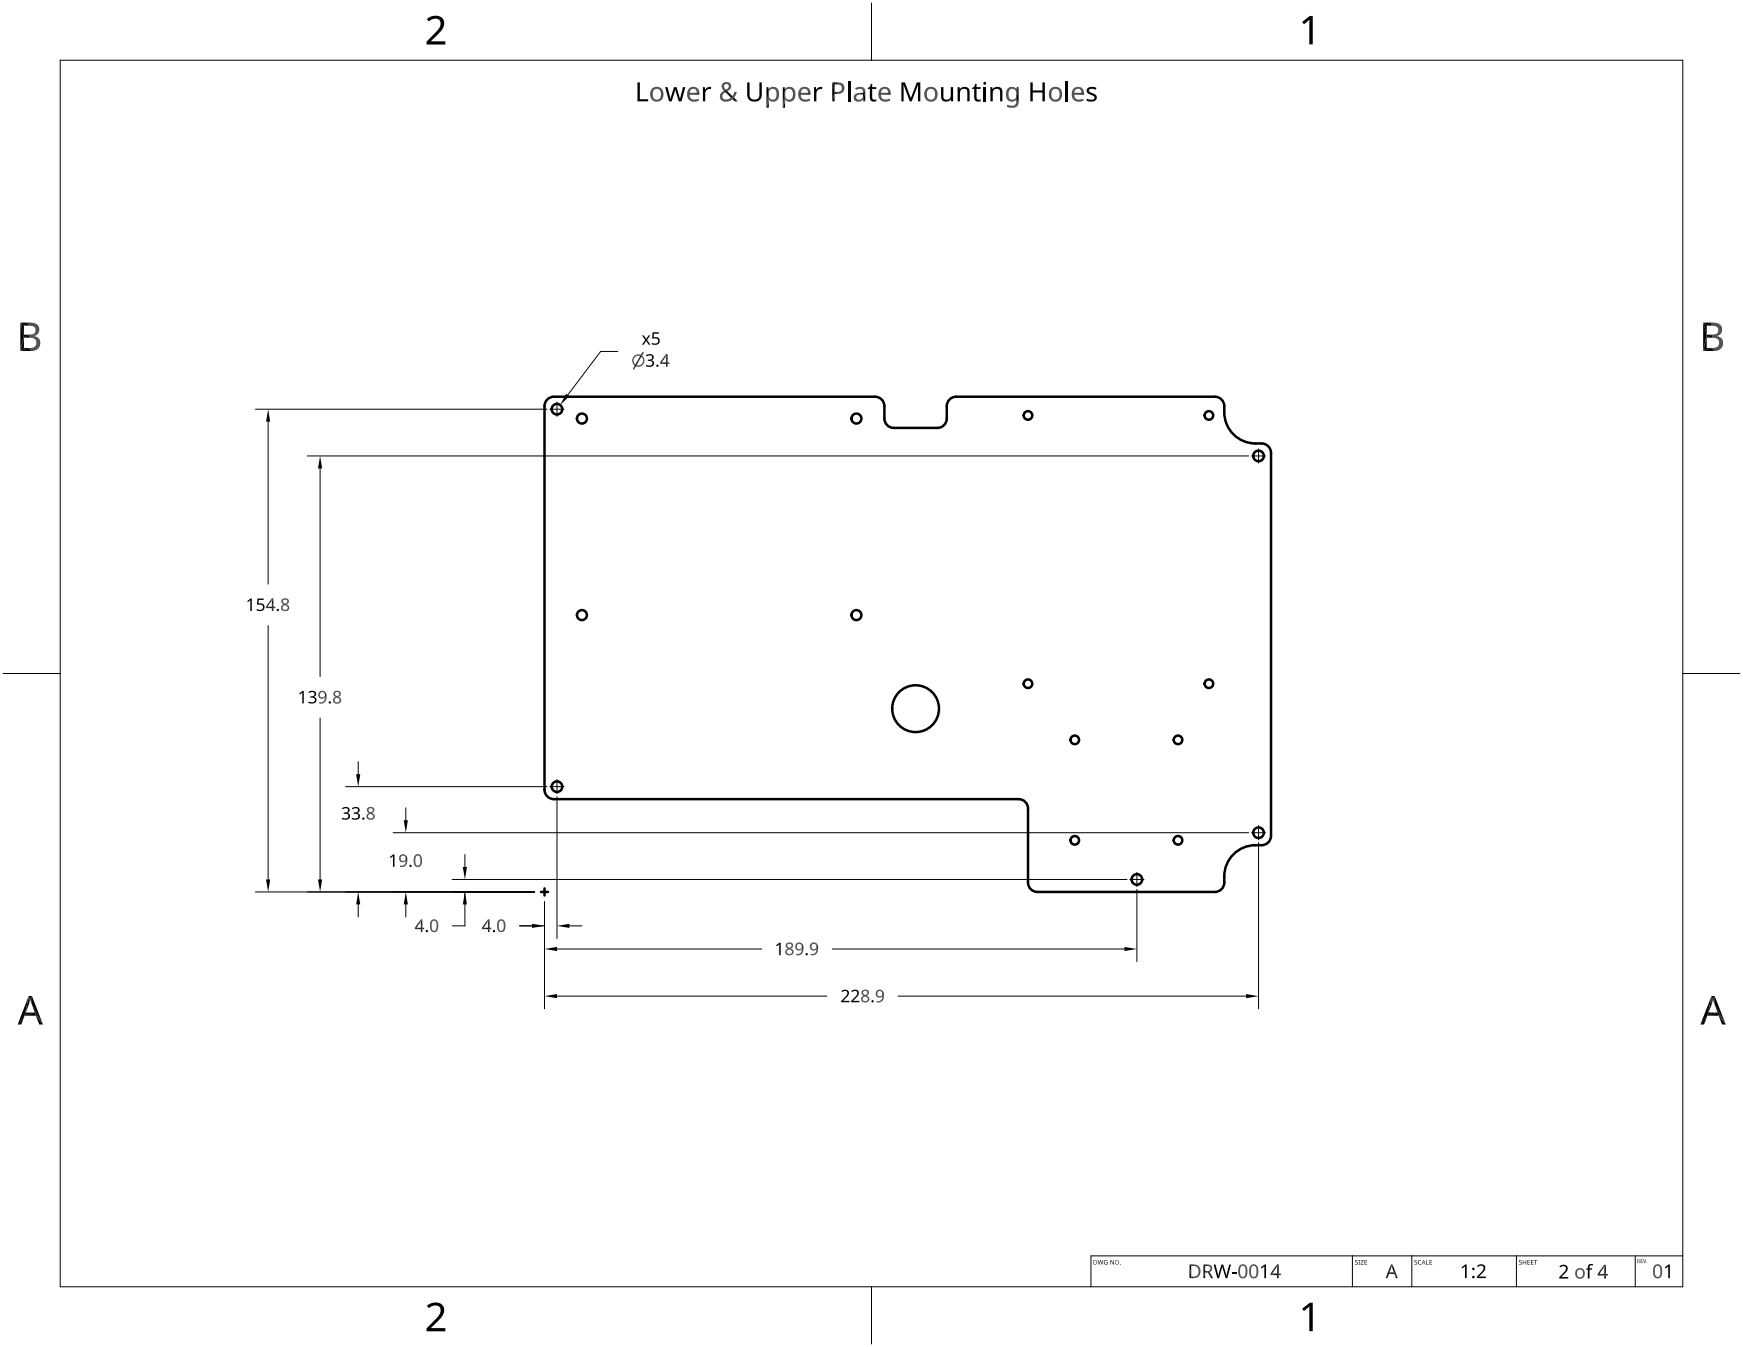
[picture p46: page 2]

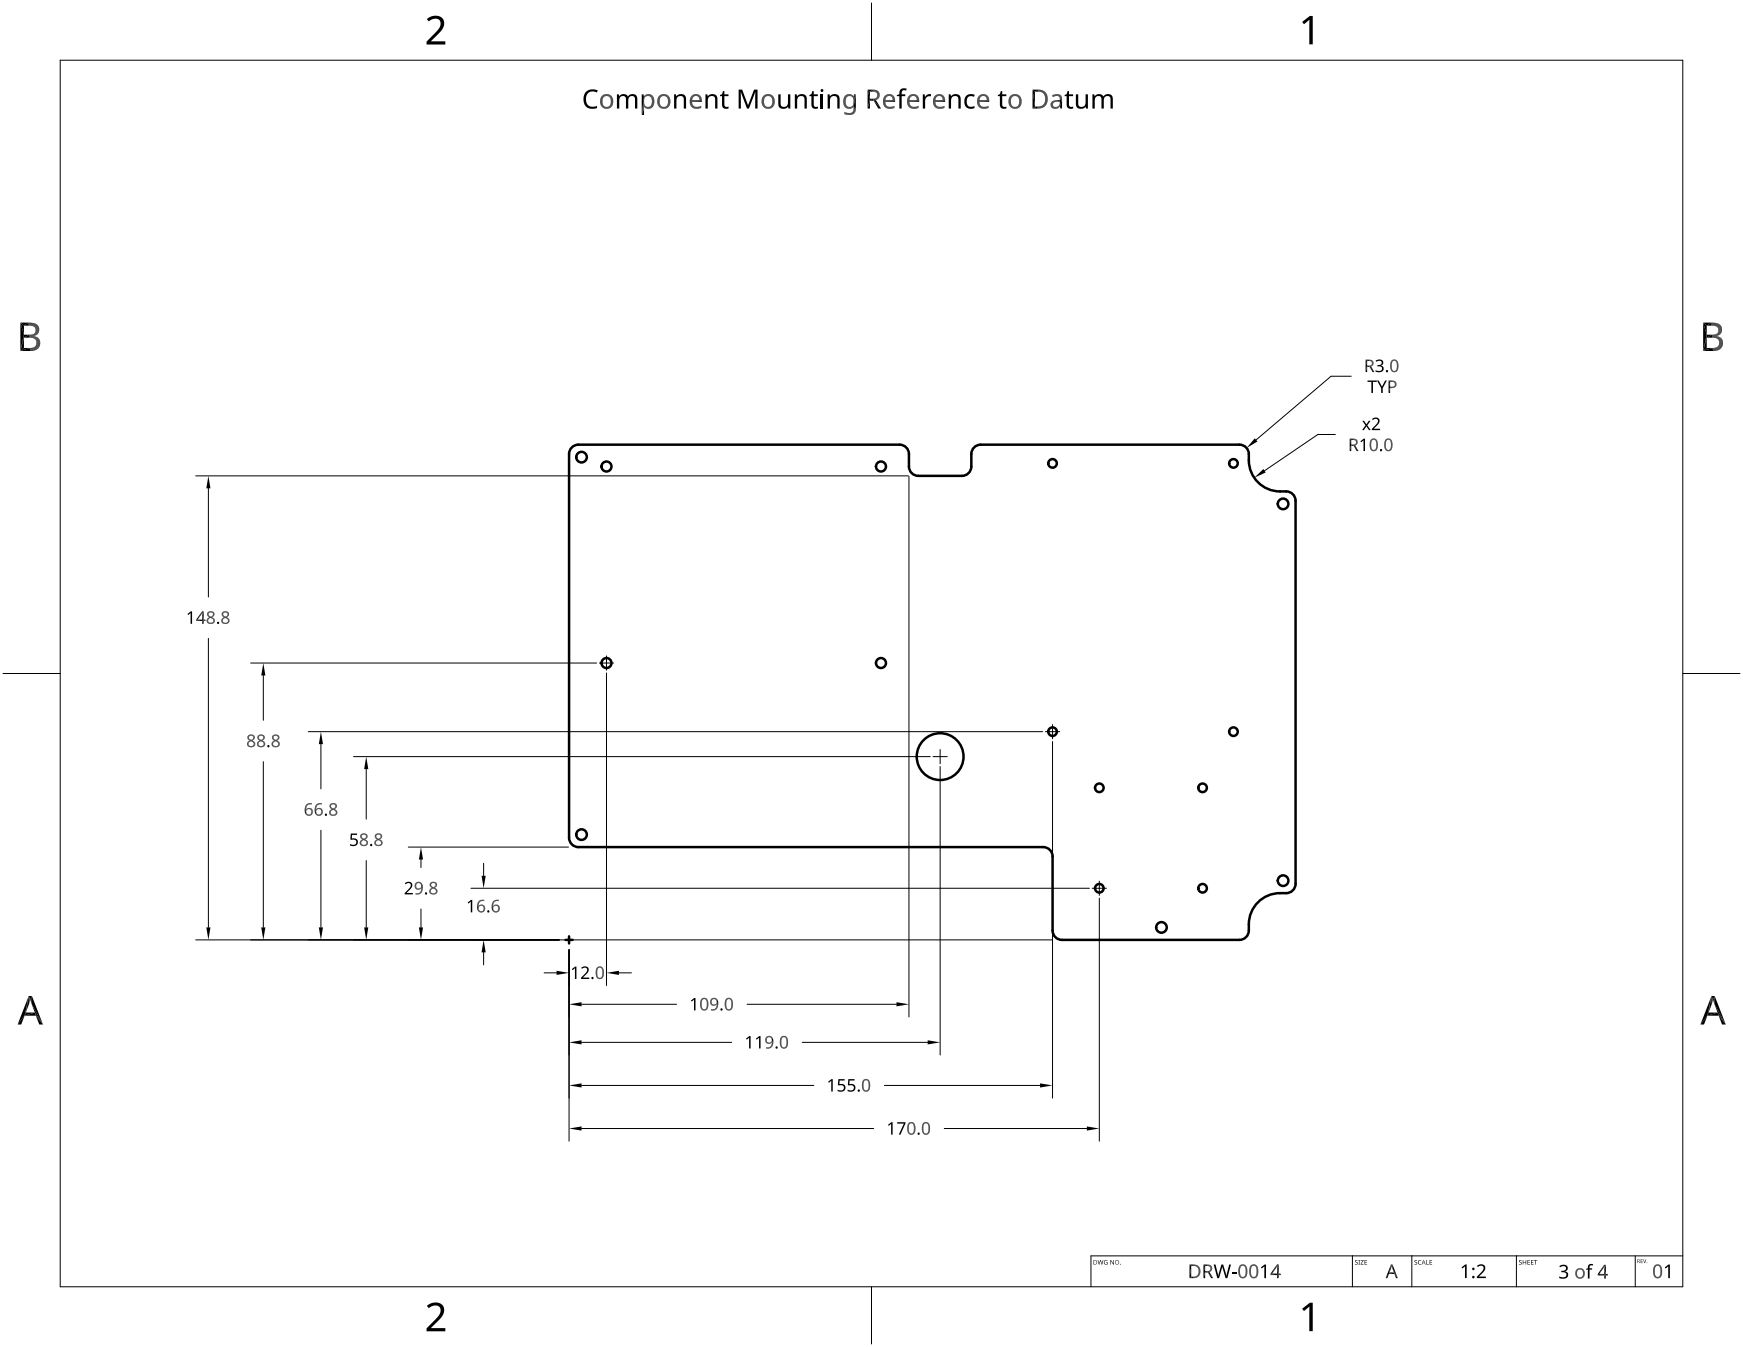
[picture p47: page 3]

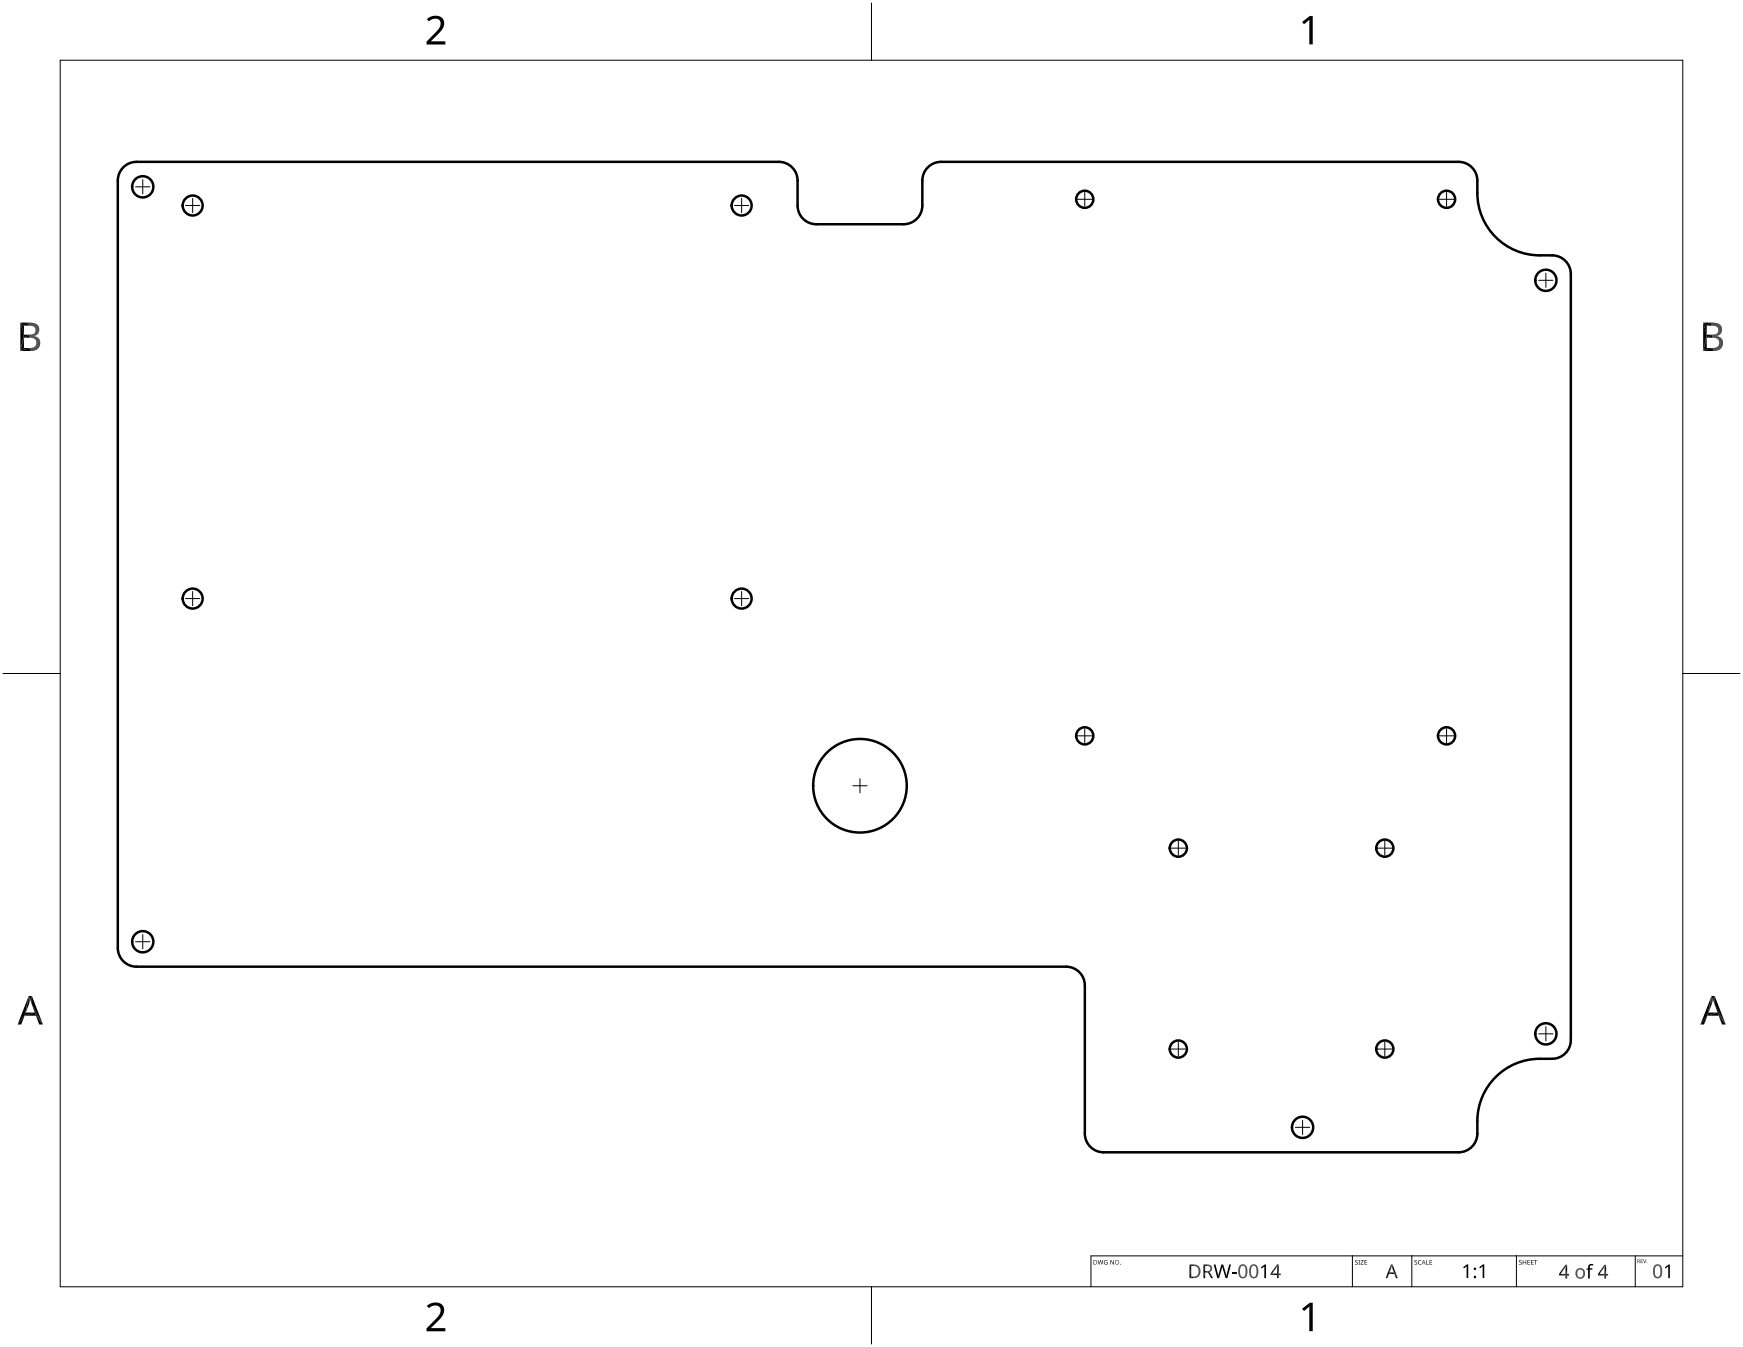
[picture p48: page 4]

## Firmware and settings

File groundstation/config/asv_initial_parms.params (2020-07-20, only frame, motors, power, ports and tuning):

1	1	ATC_SPEED_D	0.000000000000000000	9
1	1	ATC_SPEED_FF	0.000000000000000000	9
1	1	ATC_SPEED_FLTD	0.000000000000000000	9
1	1	ATC_SPEED_FLTE	10.000000000000000000	9
1	1	ATC_SPEED_FLTT	0.000000000000000000	9
1	1	ATC_SPEED_I	0.200000002980232239	9
1	1	ATC_SPEED_IMAX	1.000000000000000000	9
1	1	ATC_SPEED_P	0.200000002980232239	9
1	1	ATC_STR_ACC_MAX	180.000000000000000000	9
1	1	ATC_STR_ANG_P	2.500000000000000000	9
1	1	ATC_STR_RAT_D	0.000000000000000000	9
1	1	ATC_STR_RAT_FF	0.200000002980232239	9
1	1	ATC_STR_RAT_FLTD	0.000000000000000000	9
1	1	ATC_STR_RAT_FLTE	10.000000000000000000	9
1	1	ATC_STR_RAT_FLTT	0.000000000000000000	9
1	1	ATC_STR_RAT_I	0.200000002980232239	9
1	1	ATC_STR_RAT_IMAX	1.000000000000000000	9
1	1	ATC_STR_RAT_MAX	360.000000000000000000	9
1	1	ATC_STR_RAT_P	0.200000002980232239	9
1	1	BATT2_MONITOR	0	2
1	1	BATT3_MONITOR	0	2
1	1	BATT4_MONITOR	0	2
1	1	BATT5_MONITOR	0	2
1	1	BATT6_MONITOR	0	2
1	1	BATT7_MONITOR	0	2
1	1	BATT8_MONITOR	0	2
1	1	BATT9_MONITOR	0	2
1	1	BATT_MONITOR	0	2
1	1	FRAME_CLASS	2	2
1	1	FRAME_TYPE	0	2
1	1	INS_GYRO_FILTER	4	4
1	1	INS_HNTCH_ENABLE	0	2
1	1	MOT_PWM_FREQ	16	2
1	1	MOT_PWM_TYPE	0	2
1	1	MOT_SAFE_DISARM	0	2
1	1	MOT_SLEWRATE	100	4
1	1	MOT_SPD_SCA_BASE	1.000000000000000000	9
1	1	MOT_THR_MAX	100	2
1	1	MOT_THR_MIN	0	2
1	1	MOT_THST_EXPO	0.000000000000000000	9
1	1	MOT_VEC_THR_BASE	0.000000000000000000	9
1	1	SERIAL0_BAUD	115	6
1	1	SERIAL0_PROTOCOL	2	2
1	1	SERIAL1_BAUD	57	6
1	1	SERIAL1_OPTIONS	0	4
1	1	SERIAL1_PROTOCOL	1	2
1	1	SERIAL2_BAUD	57	6
1	1	SERIAL2_OPTIONS	0	4
1	1	SERIAL2_PROTOCOL	1	2
1	1	SERIAL3_BAUD	38	6
1	1	SERIAL3_OPTIONS	0	4
1	1	SERIAL3_PROTOCOL	5	2
1	1	SERIAL4_BAUD	38	6
1	1	SERIAL4_OPTIONS	0	4
1	1	SERIAL4_PROTOCOL	5	2
1	1	SERIAL5_BAUD	57	6
1	1	SERIAL5_OPTIONS	0	4
1	1	SERIAL5_PROTOCOL	-1	2
1	1	SERIAL6_BAUD	57	6
1	1	SERIAL6_OPTIONS	0	4
1	1	SERIAL6_PROTOCOL	-1	2
1	1	SERIAL7_BAUD	57	6
1	1	SERIAL7_OPTIONS	0	4
1	1	SERIAL7_PROTOCOL	-1	2
1	1	SERVO1_FUNCTION	74	2
1	1	SERVO1_MAX	1700	4
1	1	SERVO1_MIN	1300	4
1	1	SERVO1_REVERSED	1	2
1	1	SERVO1_TRIM	1500	4
1	1	SERVO2_FUNCTION	73	2
1	1	SERVO2_MAX	1700	4
1	1	SERVO2_MIN	1300	4
1	1	SERVO2_REVERSED	0	2
1	1	SERVO2_TRIM	1500	4
1	1	SERVO3_FUNCTION	0	2
1	1	SERVO3_MAX	1900	4
1	1	SERVO3_MIN	1100	4
1	1	SERVO3_REVERSED	0	2
1	1	SERVO3_TRIM	1500	4
1	1	SERVO4_FUNCTION	0	2
1	1	SERVO4_MAX	1900	4
1	1	SERVO4_MIN	1100	4
1	1	SERVO4_REVERSED	0	2
1	1	SERVO4_TRIM	1500	4
1	1	SERVO5_FUNCTION	0	2
1	1	SERVO5_MAX	1900	4
1	1	SERVO5_MIN	1100	4
1	1	SERVO5_REVERSED	0	2
1	1	SERVO5_TRIM	1500	4
1	1	SERVO6_FUNCTION	0	2
1	1	SERVO6_MAX	1900	4
1	1	SERVO6_MIN	1100	4
1	1	SERVO6_REVERSED	0	2
1	1	SERVO6_TRIM	1500	4
1	1	SERVO7_FUNCTION	0	2
1	1	SERVO7_MAX	1900	4
1	1	SERVO7_MIN	1100	4
1	1	SERVO7_REVERSED	0	2
1	1	SERVO7_TRIM	1500	4
1	1	SERVO8_FUNCTION	0	2
1	1	SERVO8_MAX	1900	4
1	1	SERVO8_MIN	1100	4
1	1	SERVO8_REVERSED	0	2
1	1	SERVO8_TRIM	1500	4
1	1	SERVO9_FUNCTION	0	2
1	1	SERVO9_MAX	1900	4
1	1	SERVO9_MIN	1100	4
1	1	SERVO9_REVERSED	0	2
1	1	SERVO9_TRIM	1500	4

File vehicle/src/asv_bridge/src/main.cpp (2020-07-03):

#include <asv_bridge/asv_bridge_node.hpp>

int main(int argc, char ** argv)
{
  rclcpp::init( argc, argv );
  
  spdlog::info("========================================");
  spdlog::info("STARTING asv_bridge\n");

  auto node = std::make_shared<ASVBridgeNode>();

  rclcpp::spin( node );  

  spdlog::info("ENDING asv_bridge\n");
  return 0;
}

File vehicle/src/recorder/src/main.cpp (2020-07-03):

#include <recorder/recorder_node.hpp>

int main(int argc, char ** argv)
{
  rclcpp::init( argc, argv );

  rclcpp::executors::SingleThreadedExecutor exec;
  
  spdlog::info("========================================");
  spdlog::info("STARTING recorder\n");

  auto node = std::make_shared<RecorderNode>();

  exec.add_node( node );

  while( rclcpp::ok() )
  {
    exec.spin();
  }
  
  spdlog::info("ENDING recorder\n");
  return 0;
}

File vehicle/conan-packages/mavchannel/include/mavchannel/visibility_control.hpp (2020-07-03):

#ifndef MAVCHANNEL__VISIBILITY_CONTROL_H_
#define MAVCHANNEL__VISIBILITY_CONTROL_H_

// This logic was borrowed (then namespaced) from the examples on the gcc wiki:
//     https://gcc.gnu.org/wiki/Visibility

#if defined _WIN32 || defined __CYGWIN__
  #ifdef __GNUC__
    #define MAVCHANNEL_EXPORT __attribute__ ((dllexport))
    #define MAVCHANNEL_IMPORT __attribute__ ((dllimport))
  #else
    #define MAVCHANNEL_EXPORT __declspec(dllexport)
    #define MAVCHANNEL_IMPORT __declspec(dllimport)
  #endif
  #ifdef MAVCHANNEL_BUILDING_LIBRARY
    #define MAVCHANNEL_PUBLIC MAVCHANNEL_EXPORT
  #else
    #define MAVCHANNEL_PUBLIC MAVCHANNEL_IMPORT
  #endif
  #define MAVCHANNEL_PUBLIC_TYPE MAVCHANNEL_PUBLIC
  #define MAVCHANNEL_LOCAL
#else
  #define MAVCHANNEL_EXPORT __attribute__ ((visibility("default")))
  #define MAVCHANNEL_IMPORT
  #if __GNUC__ >= 4
    #define MAVCHANNEL_PUBLIC __attribute__ ((visibility("default")))
    #define MAVCHANNEL_LOCAL  __attribute__ ((visibility("hidden")))
  #else
    #define MAVCHANNEL_PUBLIC
    #define MAVCHANNEL_LOCAL
  #endif
  #define MAVCHANNEL_PUBLIC_TYPE
#endif

#endif  // MAVCHANNEL__VISIBILITY_CONTROL_H_

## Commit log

2020-07-20 Updates vehicle setup docs with firmware and parameter flashing instructions that target Ardurover, rather than Ardusub.
    [asv_initial_parms.params]
2020-07-20 Updates BOM to v4
2020-07-20 Restructures documentation. Adds top-level readme and additional readme files. Adds note about pinger node in vehicle/software.md.
    [PRT-0013-01_upper_plate.dxf, PRT-0013-01_upper_plate.step, PRT-0015-10_power_mounting_block.step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]
2020-10-15 Fixes ros-foxy-desktop package name in groundstation setup and adds python3-wheel package
